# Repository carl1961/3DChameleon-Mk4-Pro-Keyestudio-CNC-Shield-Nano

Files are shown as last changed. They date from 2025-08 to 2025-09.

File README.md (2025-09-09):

# 3DChameleon-Mk4-Pro-Keyestudio-CNC-Shield-Nano
3DChameleon Mk4 Pro   

Controller using Keyestudio Nano CNC Shield V4 (Ks0152)  https://wiki.keyestudio.com/Ks0152_keyestudio_CNC_Shield_V4

WIN_20250906_18_50_13_Pro

WIN_20250828_07_41_26_Pro

3DChameleon_Mk4_Pro_Keyestudio_CNC_Shield_Nano v17

3DChameleon_Mk4_Pro_Keyestudio_CNC_Shield_Nano-2

## endstop micro switch 

Used for button on controller, in photo connected to Cool EN , later it will be moved to like X+ and external enstop switch on  X- those both share same D9 pin.

WIN_20250828_07_53_02_Pro

WIN_20250828_07_51_41_Pro

https://www.3dchameleon.com/old-forum/support/help-on-setup-for-cnc-shield-v4-ankermake-m5c

AMS Multi color for any 3d printer

https://github.com/3DChameleon/3DChameleonMk4

https://www.3dchameleon.com/

https://www.youtube.com/@3d_chameleon

Easy 3D Printable 4Y splitter    https://www.printables.com/model/808136-4-in-1-ptfe-adapter

Cutter Servo Board plugged into Z drive location 12V source,  stepdown to 6 Volts for servo using DD4OAJSA (adjustable ) 

!! Do voltage adjustment before plugging servo in.!!  https://alexnld.com/product/3pcs-dd40ajsa-5-40v-to-24v-12v-5v-wide-voltage-adjustable-step-down-dc-voltage-converter-power-regulator-module/

WIN_20250828_14_45_58_Pro

#Things to know

[Cotestant custom work !!](https://github.com/cotestatnt/3DChameleonMk4)

cotestatnt

I successfully built and installed a slightly modified version of the 3D Chameleon color changer on a Bambulab A1, and it works really well.
I can complete a color change in less than 20 seconds because the filament path on the A1 is very short. There is still room to improve this further, for example, by increasing the stepper motor speed.

The only aspect that didn’t fully convince me is the small teeth system for securing the PTFE tubes. So, I adapted your design to accommodate these fittings that I had available, cut in half:



(Connect Straight Union Tube Fitting, 4mm OD x 4mm OD, Straight Pneumatic Connector)

I believe there is also enough space to screw in a standard PC4-M6 fitting without any major issues.

For the electronics, I repurposed some components I had on hand, using a CNC shield for an Arduino Nano and a couple of Hall sensors instead of microswitches. I also added a sensor for homing the selector without bringing the motor to a mechanical stop, as I found it to be somewhat inaccurate—the motor tends to "bounce" when it starts skipping steps. While this isn’t a major issue, since I had the sensor available, I preferred this approach.
As for the firmware, since speed is more important to me than flexibility or the max number of possible colors, I simplified the color selection process, as I usually only need 2–3 colors for my designs.

## Jumpers and pins

KS0152_shield

## New Code by cotestatnt  https://github.com/cotestatnt/3DChameleonMk4

toolchange (Code in slicer pressing Hall sensor) or External button 

 selectionTime >= 500 && selectionTime < 1000)   Select extruder A

 selectionTime >= 1000 && selectionTime < 1500)  Select extruder B

 selectionTime >= 1500 && selectionTime < 2000)  Select extruder C
 
 selectionTime >= 2000 && selectionTime < 2500)  Select extruder D 

 selectionTime >= 3200)                          home sequence

 

## Selecter (Hall Sensor) 

tool_selector2

## KY-003 Hall Sensor



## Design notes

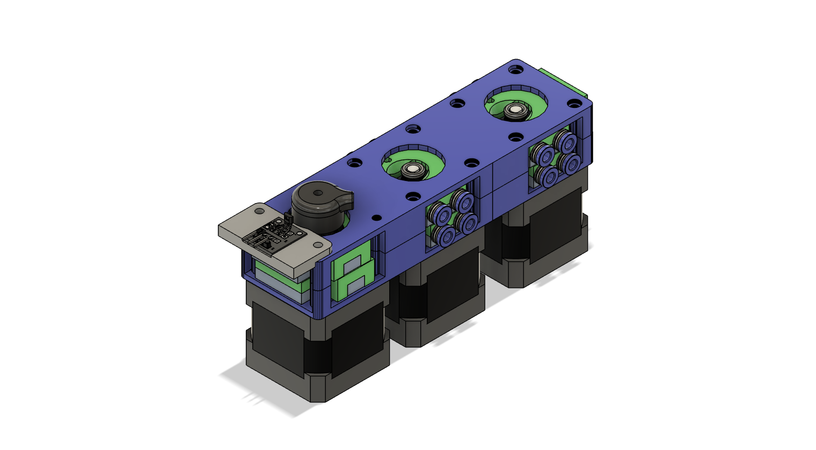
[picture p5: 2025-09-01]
3DChameleon-Mk4-8-Color v21.png

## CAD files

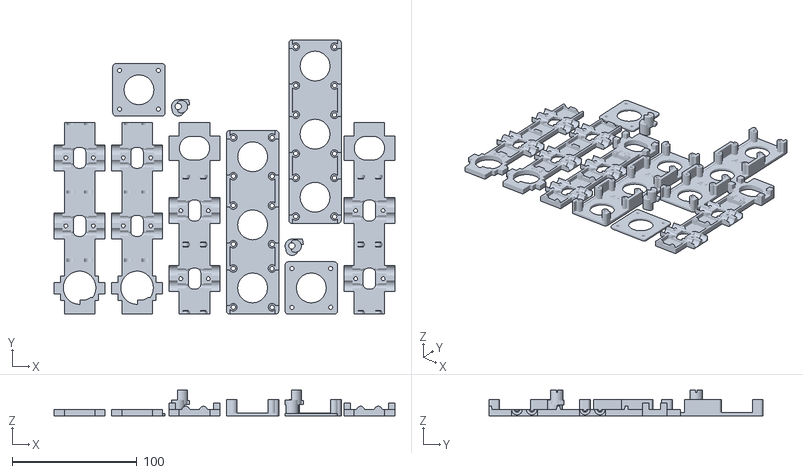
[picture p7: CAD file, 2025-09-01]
STL/3DChameleon 4.0 (8 color) (coupling)(FULL SET).stl
273.0 x 219.6 x 20.5

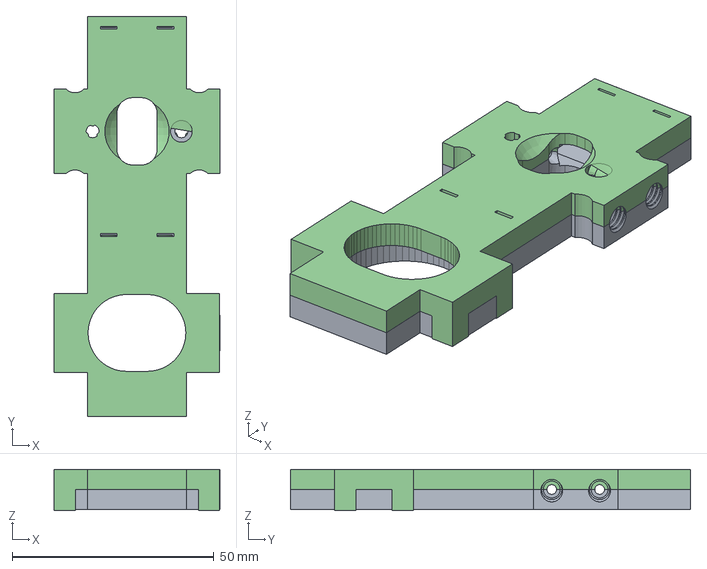
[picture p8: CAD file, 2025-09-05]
CAD/3DChameleon 4.0 (B Part C Part) (4 color) (PC4-M6).step
41.0 x 99.1 x 10.2 mm

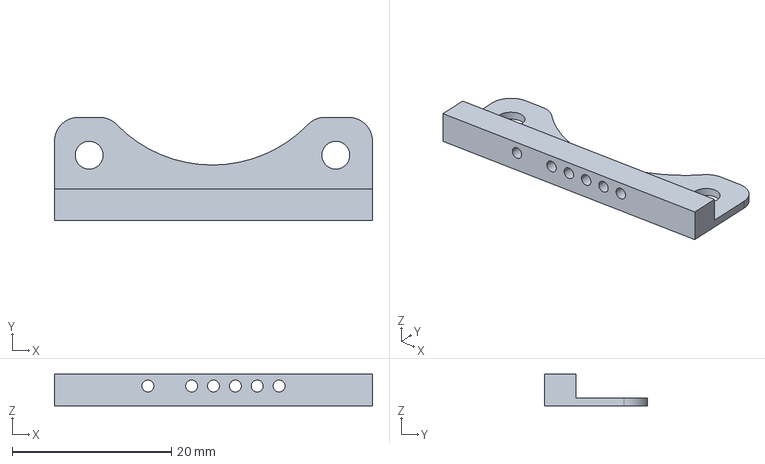
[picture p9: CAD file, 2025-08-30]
cotestatnt custom 3DChameleonMk4-main/3DChameleon (home sensor bracket).step
40.0 x 13.0 x 4.00 mm

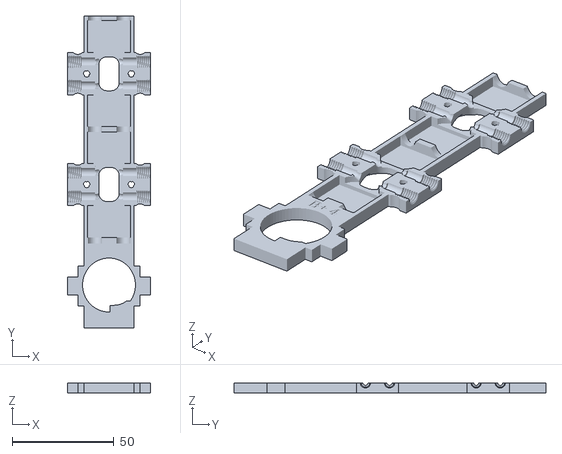
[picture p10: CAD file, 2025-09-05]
STL/3DChameleon 4.0 (B Part) (8 color) (PC4-M6).stl
41.0 x 153.6 x 5.00

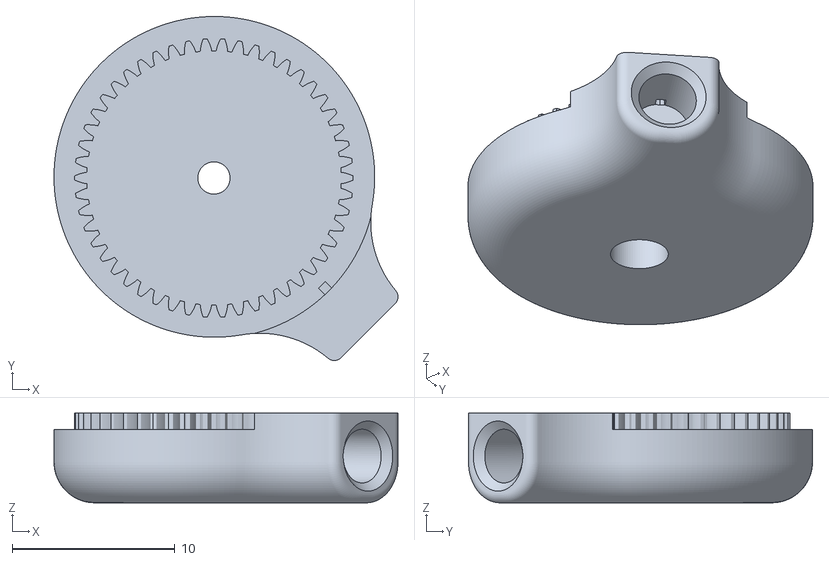
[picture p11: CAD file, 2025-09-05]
STL/Homing Parts/3DChameleon 4.0 (Magnet) (slip grooves).stl
21.1 x 21.1 x 5.50

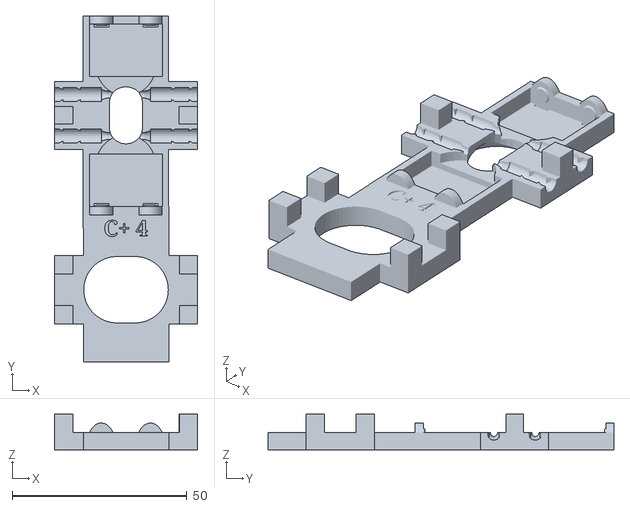
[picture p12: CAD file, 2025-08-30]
STL/Original/3DChameleon 4.0 (C Part).stl
41.0 x 99.1 x 10.2

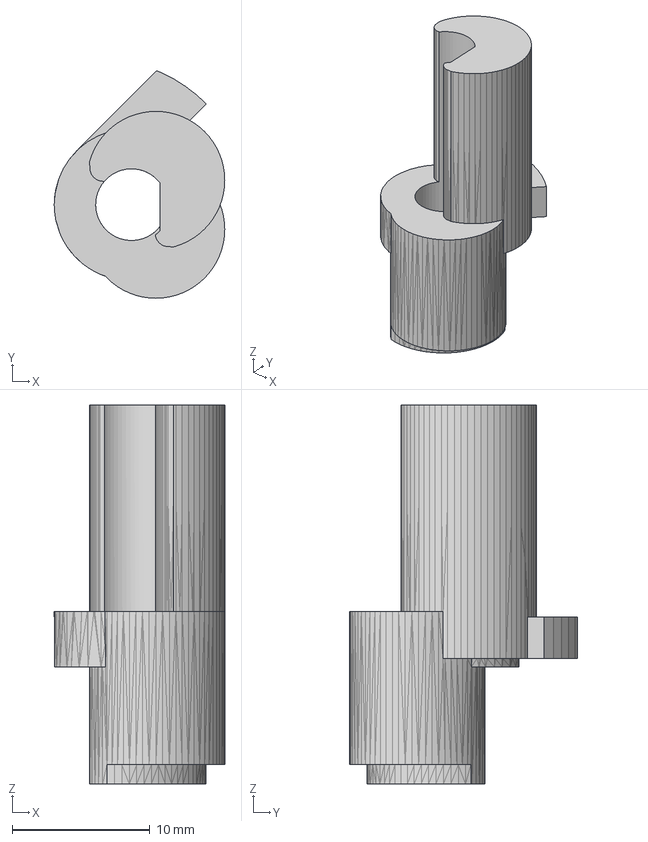
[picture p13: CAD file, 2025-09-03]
CAD/3DChameleon 4.0 (Cam) (Homing Magnet)_.step
12.4 x 16.5 x 27.5 mm

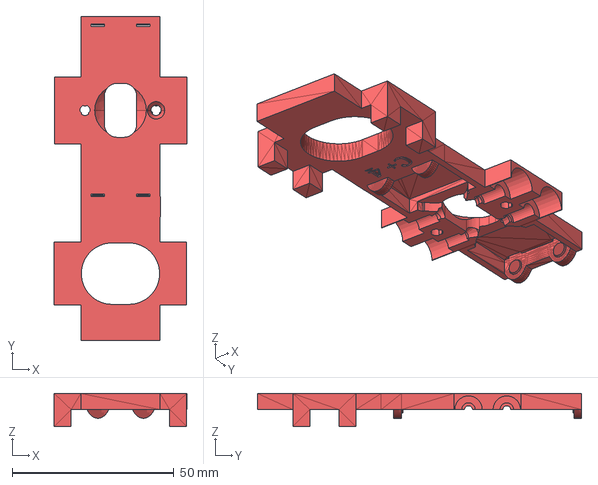
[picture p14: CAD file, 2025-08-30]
cotestatnt custom 3DChameleonMk4-main/3DChameleon 4.0 (C Part).step
41.0 x 100.3 x 10.2 mm

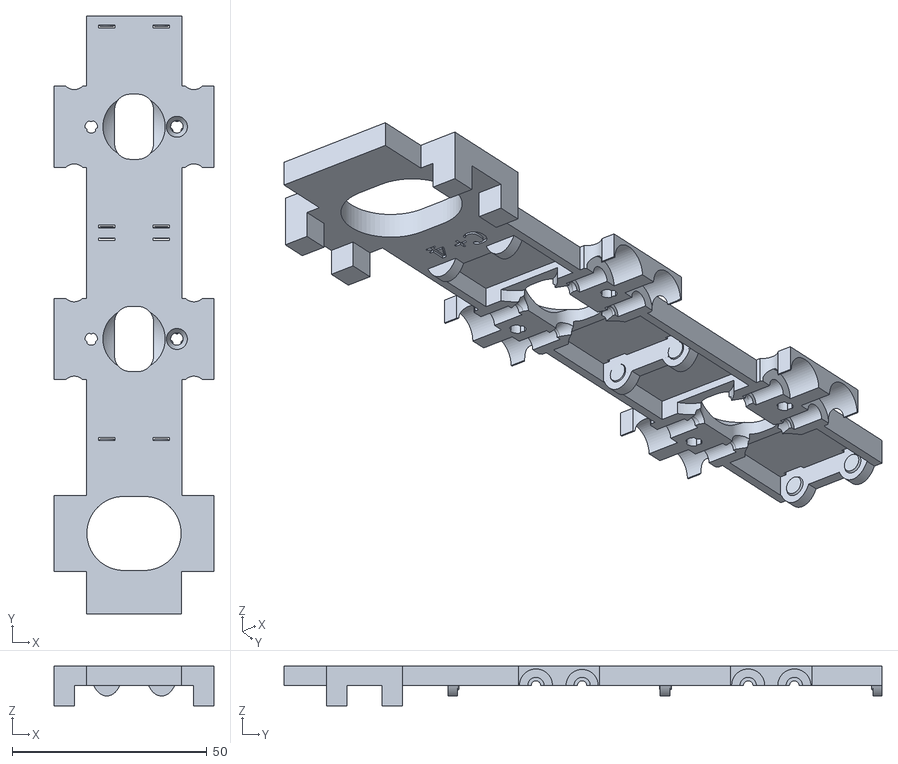
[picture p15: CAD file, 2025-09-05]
STL/3DChameleon 4.0 (C Part) (8 color) (couplings) V2.stl
41.0 x 153.6 x 10.2

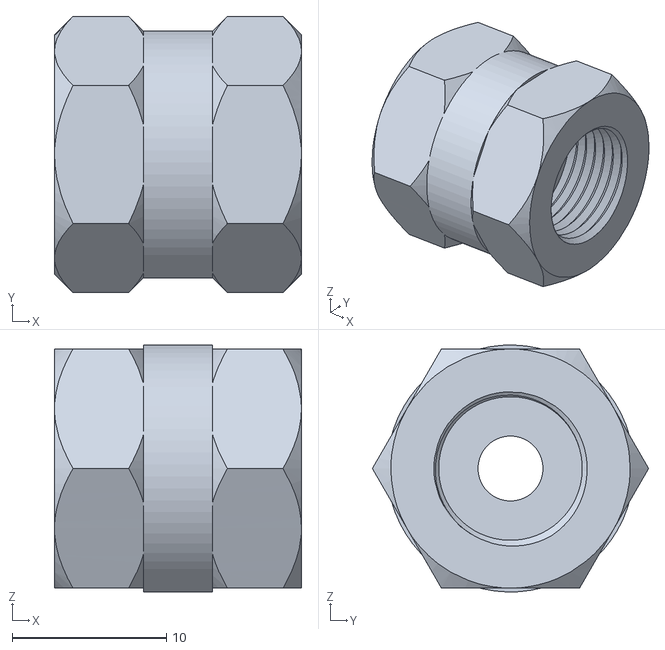
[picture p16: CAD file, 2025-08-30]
STL/Original/3DChameleon_PC4-M10_PTFE_Coupler.stl
16.0 x 17.9 x 16.0

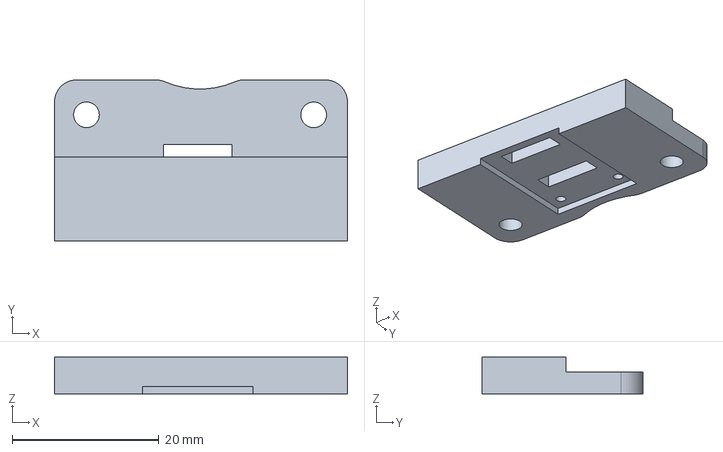
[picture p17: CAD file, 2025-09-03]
CAD/3DChameleon (home sensor bracket) v2.step
40.0 x 22.0 x 5.00 mm

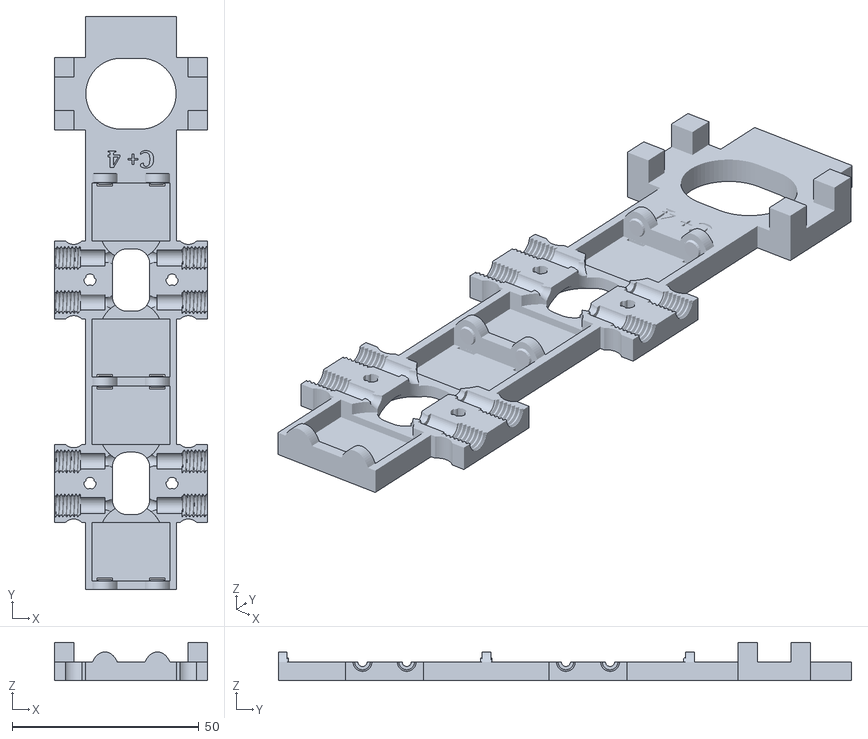
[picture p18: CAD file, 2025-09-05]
STL/3DChameleon 4.0 (C Part) (8 color) (PC4-M6).stl
41.0 x 153.6 x 10.2

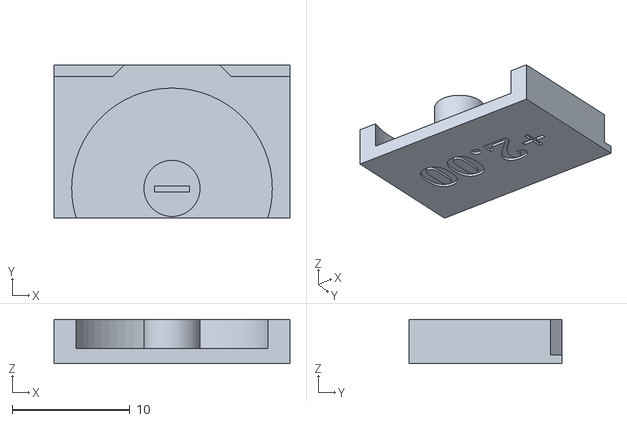
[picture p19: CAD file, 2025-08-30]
STL/Original/3DChameleon 4.0 (Bearing Carrier).stl
20.0 x 13.0 x 3.75

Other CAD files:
STL/Homing Parts/3DChameleon 4.0 (Magnet) (slip grooves)-V2.stl
cotestatnt custom 3DChameleonMk4-main/3DChameleon (home sensor bracket) v1.stl
STL/Homing Parts/3DChameleon 4.0 (Cam) (Magnet).stl
CAD/3DChameleon 4.0 (Magnet) (slip grooves) v2.step
cotestatnt custom 3DChameleonMk4-main/3DChameleon 4.0 (C Part) v1.stl
CAD/3DChameleon 4.0 (Magnet-Mount) (slip grooves) v2.step
STL/3DChameleon (home sensor bracket) v2.stl
STL/3DChameleon 4.0 (8 color) (coupling)(SET).stl
STL/3DChameleon 4.0 (A Part) (8 color).stl
STL/3DChameleon 4.0 (B Part) (4 color) (PC4-M6).stl
STL/3DChameleon 4.0 (B Part) (8 color) (coupling) V2.stl
STL/3DChameleon 4.0 (B Part) (8 color) (coupling).stl
STL/3DChameleon 4.0 (C Part) (4 color) (PC4-M6).stl
STL/3DChameleon 4.0 (C Part) (8 color) (couplings).stl
STL/3DChameleon 4.0 (C Part) (8 color).stl
STL/3DChameleon 4.0 (Cam) (v2).stl
STL/3DChameleon-Mk4-8-Color-Model.stl
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

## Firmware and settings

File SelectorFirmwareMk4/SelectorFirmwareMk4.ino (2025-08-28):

// November 28, 2024

/* 3DChameleon Mk4.1 Firmware

Copyright 2024 William J. Steele

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
Single Button Press Commands (count pulses of selector)

#1 - 1
#2 - 2
#3 - 3
#4 - 4
#5 - Home and Load
#6 - Unload Last and Home
#7 - Home
#8 - Next Filament
#9 - Random Filament
 
*/

#include <SSD1306Ascii.h> //i2C OLED
#include <SSD1306AsciiWire.h> //i2C OLED
#include <SparkFunSX1509.h> // sparkfun i/o expansion board - used for additional filament sensors as well as communications with secondary boards
#include <Wire.h>
#include <SPI.h>
#include <Servo.h>

#define SCREEN_WIDTH 128 // OLED display width, in pixels
#define SCREEN_HEIGHT 64 // OLED display height, in pixels

/**
 * Made with Marlin Bitmap Converter
 * https://marlinfw.org/tools/u8glib/converter.html
 *
 * This bitmap from 128x64 pasted image
 */
#pragma once

const unsigned char bitmap_logo[] PROGMEM = {
  B00000000,B00000000,B00000000,B00000000,B00000000,B00000000,B00000000,B00000000,B00000000,B00000000,B00000000,B00000000,B00000000,B00000000,B00000000,B00000000,
  B00000000,B00000000,B00000000,B00000000,B00000000,B00000000,B00000000,B00000000,B00000000,B00000000,B00000000,B00000000,B00000000,B00000000,B00000000,B00000000,
  B00000000,B00000000,B00000000,B00000000,B00000000,B00000000,B00000000,B00000000,B00000000,B00000000,B00000000,B00000000,B00000000,B00000000,B00000000,B00000000,
  B00000000,B00000000,B00000000,B00000000,B00000000,B00000000,B00000000,B00000000,B00000000,B00000000,B00000000,B00000000,B00000000,B00000000,B00000000,B00000000,
  B00000000,B00000000,B00000000,B00000000,B00000000,B00000000,B00000000,B00001000,B00000000,B00000000,B00000000,B00000000,B00000000,B00000000,B00000000,B00000000,
  B00000000,B00000000,B00000000,B00000000,B00000000,B00000000,B00110000,B00001100,B00100000,B00000000,B00000000,B00000000,B00000000,B00000000,B00000000,B00000000,
  B00000000,B00000000,B00000000,B00000000,B00000000,B00000000,B01111100,B00001110,B00110000,B00011100,B00000000,B00000000,B00000000,B00000000,B00000000,B00000000,
  B00000000,B00000000,B00000000,B00000000,B00000000,B00000000,B01111111,B00011111,B01111000,B00011111,B00000000,B00000000,B00000000,B00000000,B00000000,B00000000,
  B00000000,B00000000,B00000000,B00000000,B00000000,B00000000,B01111111,B10011111,B11111000,B00011111,B10000000,B00000000,B00000000,B00000000,B00000000,B00000000,
  B00000000,B00000000,B00000000,B00000000,B00000000,B00000000,B01111111,B11011111,B11110110,B00011111,B11000000,B00000000,B00000000,B00000000,B00000000,B00000000,
  B00000000,B00000000,B00000000,B00000000,B00000000,B00000000,B01111111,B10000000,B00000110,B00011111,B11100000,B00000000,B00000000,B00000000,B00000000,B00000000,
  B00000000,B00000000,B00000000,B00000000,B00000000,B11111100,B01111101,B11111111,B11110010,B00111111,B11110000,B00000000,B00000000,B00000000,B00000000,B00000000,
  B00000000,B00000000,B00000000,B00000000,B00000000,B11111111,B00001111,B11111111,B11111110,B00111111,B11111000,B00000000,B00000000,B00000000,B00000000,B00000000,
  B00000000,B00000000,B00000000,B00000000,B00000000,B01111111,B00111111,B11111111,B11111111,B00111111,B11111100,B00000000,B00000000,B00000000,B00000000,B00000000,
  B00000000,B00000000,B00000000,B00000000,B00000000,B01111110,B00111111,B11111111,B11111111,B01111111,B11111100,B00000000,B00000000,B00000000,B00000000,B00000000,
  B00000000,B00000000,B00000000,B00000000,B00000000,B01111101,B11111111,B11111111,B11111111,B01111111,B11111110,B00000000,B00000000,B00000000,B00000000,B00000000,
  B00000000,B00000000,B00000000,B00000000,B00000000,B01111011,B11111111,B11111111,B11111110,B11111111,B11111110,B00000000,B00000000,B00000000,B00000000,B00000000,
  B00000000,B00000000,B00000000,B00000000,B00000000,B01100111,B11101111,B11111111,B11111111,B11111111,B11111110,B00000000,B00000000,B00000000,B00000000,B00000000,
  B00000000,B00000000,B00000000,B00000000,B00000111,B10001111,B11110111,B11111111,B11111111,B11111111,B11111111,B00000000,B00000000,B00000000,B00000000,B00000000,
  B00000000,B00000000,B00000000,B00000000,B00001111,B10111111,B11111011,B11111111,B11111101,B11111110,B00011111,B00000000,B00000000,B00000000,B00000000,B00000000,
  B00000000,B00000000,B00000000,B00000000,B00001111,B10111111,B11111001,B11111111,B11111111,B11111100,B00001111,B00000000,B00000000,B00000000,B00000000,B00000000,
  B00000000,B00000000,B00000000,B00000000,B00001111,B01111111,B11111101,B11111111,B11111111,B11111001,B11110111,B00000000,B00000000,B00000000,B00000000,B00000000,
  B00000000,B00000000,B00000000,B00000000,B00000111,B11111111,B11111110,B11111111,B11111111,B11111011,B11110011,B00000000,B00000000,B00000000,B00000000,B00000000,
  B00000000,B00000000,B00000000,B00000000,B00000010,B11111111,B11111110,B11111111,B11111111,B11111011,B10111011,B00000000,B00000000,B00000000,B00000000,B00000000,
  B00000000,B00000000,B00000000,B00000000,B00111100,B11111111,B11111111,B01111111,B11111111,B11111011,B11110011,B00000000,B00000000,B00000000,B00000000,B00000000,
  B00000000,B00000000,B00000000,B00000000,B01111101,B11111111,B11111111,B01111111,B11111111,B11111001,B11110111,B00000000,B00000000,B00000000,B00000000,B00000000,
  B00000000,B00000000,B00000000,B00000000,B01111101,B11111111,B11111111,B10111111,B11111101,B11111100,B11101111,B00000000,B00000000,B00000000,B00000000,B00000000,
  B00000000,B00000000,B00000000,B00000000,B00111101,B11111111,B11111111,B10000000,B00000000,B11111111,B11011111,B00000000,B00000000,B00000000,B00000000,B00000000,
  B00000000,B00000000,B00000000,B00000000,B00011001,B11111111,B11111111,B10000000,B00000000,B11111111,B11111111,B00000000,B00000000,B00000000,B00000000,B00000000,
  B00000000,B00000000,B00000000,B00000000,B00001011,B11111111,B11111111,B01100000,B00000000,B01111111,B11111111,B00000000,B00000000,B00000000,B00000000,B00000000,
  B00000000,B00000000,B00000000,B00000000,B00000001,B11111111,B11111110,B11111000,B00000000,B00111111,B11111111,B00000000,B00000000,B00000000,B00000000,B00000000,
  B00000000,B00000000,B00000000,B00000000,B00011010,B01111111,B11111101,B11111110,B00000000,B00001111,B11111110,B00000000,B00000000,B00000000,B00000000,B00000000,
  B00000000,B00000000,B00000000,B00000000,B01111011,B11100111,B11111011,B11111110,B00000000,B00000111,B11111110,B00000000,B00000000,B00000000,B00000000,B00000000,
  B00000000,B00000000,B00000000,B00000000,B11111011,B11111100,B01110000,B01111111,B00000000,B00000001,B11111110,B00000000,B00000000,B00000000,B00000000,B00000000,
  B00000000,B00000000,B00000000,B00000000,B01111011,B11111111,B00000000,B01111111,B10000000,B00000000,B01111100,B00000000,B00000000,B00000000,B00000000,B00000000,
  B00000000,B00000000,B00000000,B00000000,B00011011,B11111111,B11000000,B11111111,B11111000,B00000000,B00000000,B00000000,B00000000,B00000000,B00000000,B00000000,
  B00000000,B00000000,B00000000,B00000000,B00001011,B11111111,B11100001,B11111111,B11111110,B00000000,B00000000,B00000000,B00000000,B00000000,B00000000,B00000000,
  B00000000,B00000000,B00000000,B00000000,B00111011,B11111111,B11100001,B11111111,B11111111,B00000000,B00000000,B00000000,B00000000,B00000000,B00000000,B00000000,
  B00000000,B00000000,B00000000,B00000000,B01111011,B11111111,B11100011,B11111111,B11110011,B10000000,B00000000,B00000000,B00000000,B00000000,B00000000,B00000000,
  B00000000,B00000000,B00000000,B00000000,B11111011,B11111111,B11100000,B00000001,B11111100,B00000000,B00000000,B00000000,B00000000,B00000000,B00000000,B00000000,
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
};


// Declaration for an SSD1306 display connected to I2C (SDA, SCL pins)
#define OLED_RESET  -1 // Reset pin # (or -1 if sharing Arduino reset pin)
#define OLED_I2C_ADDRESS 0x3C
SSD1306AsciiWire oled;

// define sparkfun io expansion
const byte SX1509_ADDRESS = 0x3E; // SX1509 I2C address
#define SX1509_FILAMENT_0 0
#define SX1509_FILAMENT_1 1
#define SX1509_FILAMENT_2 2
#define SX1509_FILAMENT_3 3
#define SX1509_OUTPUT 4
SX1509 io;                        // Create an SX1509 object to be used throughout


// defines pins numbers - Keyestudio Nano CNC shield v4 Board
#define extEnable 8
#define extStep 2
#define extDir 5

#define selEnable 8
#define selStep 3
#define selDir 6

#define trigger 9 //End Stop Switch (Black/White, do not connect red wire)  X+  Button X-
#define s_limit A4
#define filament A5

// defines pins numbers - 3D Chameleon Board
//#define extEnable 0
//#define extStep 1
//#define extDir 2

//#define selEnable A0
//#define selStep A1
//#define selDir A2

//#define trigger A3
//#define s_limit A4
//#define filament A5


const int counterclockwise = HIGH;
const int clockwise = !counterclockwise;

const int stepsPerRev = 200;
const int microSteps = 16;
const int speedDelay = 170;

const int defaultBackoff = 10;

Servo filamentCutter;  // create servo object to control a servo
int cutterPos = 0;    // variable to store the servo position
bool reverseServo = true;

int currentExtruder = -1;
int nextExtruder = 0;
int lastExtruder = -1;
int tempExtruder = -1;

int seenCommand = 0;
int prevCommand = 0;

int loaderMode = 2;  //(0= direct drive, 1=loader/unloader, 2=loader/unloader with press)

long triggerTime = 300;
long pulseTime = (triggerTime / 2);

long distance = 10;

long unloadDistance = stepsPerRev * microSteps * distance;  // this is 10 revs - about 10"
long loadDistance   = unloadDistance * 1.1;           // this is 11 revs - about 11"

int address = 0;
byte value;

long idleCount = 0;
bool logoActive = false;
bool T0Loaded = false;
bool T1Loaded = false;
bool T2Loaded = false;
bool T3Loaded = false;


bool displayEnabled = false;
bool ioEnabled = false;
//int sensorEnabled = 0;

long randomNumber = 0;

void setup()
{

  Wire.begin(); //start i2C  
	Wire.setClock(400000L); //set clock

  // set up IO expander
  if (io.begin(SX1509_ADDRESS) == true)
  {
    io.pinMode(SX1509_FILAMENT_0, INPUT_PULLUP);
    io.pinMode(SX1509_FILAMENT_1, INPUT_PULLUP);
    io.pinMode(SX1509_FILAMENT_2, INPUT_PULLUP);
    io.pinMode(SX1509_FILAMENT_3, INPUT_PULLUP);
    io.pinMode(SX1509_OUTPUT, OUTPUT);
    ioEnabled = true;
  }

  // enable OLED display
  oled.begin(&Adafruit128x64, OLED_I2C_ADDRESS);

  // wait for it to start up
  delay(50);
    

  // welcome screen
  oled.setFont(Adafruit5x7);
  oled.clear(); //clear display
	oled.println("");
  oled.println("       Welcome!"); //print a welcome message  
  oled.println("");
  oled.println("    3DChameleon Mk4"); //print a welcome message
  oled.println("");
  oled.println("         Pro");
  delay(3000);

  displayText(0, "       Ready!");
  
  seenCommand = 0;

  // Sets the two pins as Outputs
  pinMode(extEnable, OUTPUT);
  pinMode(extStep, OUTPUT);
  pinMode(extDir, OUTPUT);

  pinMode(selEnable, OUTPUT);
  pinMode(selStep, OUTPUT);
  pinMode(selDir, OUTPUT);

  // set up the button
  pinMode(trigger, INPUT_PULLUP);  // selector

  // a little override here... we're using the two inputs as I2C instead
  pinMode(s_limit, OUTPUT);    
  pinMode(filament, OUTPUT); 

  // lock the selector by energizing it
  digitalWrite(selEnable, HIGH);

  // make sure filament isn't blocked by gillotine
  connectGillotine();
  cutFilament();
  disconnectGillotine();
  
  prevCommand = 0;

}

int lastLoop = 0;

void loop()
{
  static uint32_t lastTime = 0;

  seenCommand = 0;
  idleCount++;

  // process button press
  if (digitalRead(trigger) == 0)
  {
    idleCount = 0;
    logoActive = false;
    unsigned long nextPulse;
    unsigned long pulseCount = 0;
    unsigned long commandCount = 0;

    // keep counting (and pulsing) until button is released
    while (digitalRead(trigger) == 0)
    {
      if(pulseCount<pulseTime)
      {
        pulseCount++;
        displayCommand(pulseCount);
        if(pulseCount>1) vibrateMotor();
      }
      delay(400);  // each pulse is 400+ milliseconds apart 
    }
    processCommand(pulseCount); // ok... execute whatever command was caught (by pulse count)
    pulseCount = 0;
  }

  // updates IO block, duh!  No really, grabs the state of the sparkfun gpio expansion
  updateIOBlock();

  // each loop adds 50ms delay, so that gets added AFTER the command is processed before the next one can start
  delay(50);
}

// read the sparkfun SX1509 io
void updateIOBlock()
{
    if(ioEnabled)
    {
      T0Loaded = io.digitalRead(SX1509_FILAMENT_0);
      T1Loaded = io.digitalRead(SX1509_FILAMENT_1);
      T2Loaded = io.digitalRead(SX1509_FILAMENT_2);
      T3Loaded = io.digitalRead(SX1509_FILAMENT_3);
    }
}

// display command for each button pulse
void displayCommand(long commandCount)
{

  switch(commandCount)
  {
  case 2:
    displayText(25, "    Switch to T0");
    break;
  case 3:
    displayText(25, "    Switch to T1");
    break;
  case 4:
    displayText(25, "    Switch to T2");
    break;
  case 5:
    displayText(25, "    Switch to T3");
    break;
  case 6:
    displayText(25, "    Home/Load T0");
    break;
  case 7:
    displayText(28, "    Unload/Home");
    break;
  case 8:
    displayText(50, "        Home");
    break;  
  case 9:
    displayText(50, "        Next");
    break;
  case 10:
    displayText(40, "       Random");
    break;
  default:
    displayText(30, "     No Command");
    break;
  }
}

// execute the pulse count command
void processCommand(long commandCount)
{

  // select case for commands
  switch (commandCount)
  {
  case 2: // unload current, switch to #0, load
    displayText(30, "     T0 Selected");
    currentExtruder = 0;
    processMoves();
    displayText(35, "      Idle - T0");
    break;

  case 3: // unload current, switch to #1, load
    displayText(30, "     T1 Selected");
    currentExtruder = 1;
    processMoves();
    displayText(35, "      Idle - T1");
    break;

  case 4: // unload current, switch to #3, load
    displayText(30, "     T2 Selected");
    currentExtruder = 2;
    processMoves();
    displayText(35, "      Idle - T2");
    break;

  case 5: // unload current, switch to #4, load
    displayText(30, "     T3 Selected");
    currentExtruder = 3;
    processMoves();
    displayText(35, "      Idle - T3");
    break;

  case 6: //home and reload #1
    displayText(40, "      Homing...");
    homeSelector();
    displayText(15, "   Press to Load T0");
    gotoExtruder(0, 0);
    if(loaderMode>0)rotateExtruder(clockwise, loadDistance);
    if(loaderMode>0)gotoExtruder(0, 1);
    currentExtruder = 0;
    lastExtruder = 0;
    displayText(35, "      Idle - T0");
    break;
    
  case 7: // unload current and rehome selector
    displayText(30, "     Cutting...");
    connectGillotine();
    cutFilament();
    switch(lastExtruder)
    {
      case 0:
        displayText(10, "  Press to Unload T0");
        break;
      case 1:
        displayText(10, "  Press to Unload T1");
        break;
      case 2:
        displayText(10, "  Press to Unload T2");
        break;
      case 3:
        displayText(10, "  Press to Unload T3");
        break;
    } 
    if(loaderMode>0)gotoExtruder((lastExtruder==3?2:lastExtruder+1),lastExtruder);
    if(lastExtruder<2)
    {
      if(loaderMode>0)rotateExtruder(counterclockwise, unloadDistance);
    }
    else
    {
      if(loaderMode>0)rotateExtruder(clockwise, unloadDistance);
    }
    disconnectGillotine();
    displayText(50, "        Idle");
    break;

  case 8:  
    displayText(40, "     Homing...");
    homeSelector();
    displayText(50, "        Idle");
    break;

  case 9: // move to next available filament
    displayText(30, "     Cutting...");
    connectGillotine();
    cutFilament();
    displayText(30, "     Next Tool");
    currentExtruder++;
    if(currentExtruder==4)currentExtruder=0;
    processMoves();
    displayText(35, "        Idle");
    break;

  case 10: // move to a random filament
    displayText(30, "     Cutting...");
    connectGillotine();
    cutFilament();
    displayText(30, "    Random Tool");

    // select a random number
    randomNumber = random(0,2) + 1;

    // skip ahead that many tools
    for(long i=0; i<randomNumber; i++)
    {
      currentExtruder++;
      if(currentExtruder==4)currentExtruder=0;
    }
    processMoves();
    displayText(50, "        Idle");
    break;
    
  default:
    displayText(47, "       Clear");
    delay(200);

    displayText(50, "        Idle");
    break;
  }
}

// just the routine to update the OLED
void displayText(int offset, String str)
{

  //if(displayEnabled){
    oled.clear();
    oled.println("");
    oled.println("   3DChameleon Mk4"); //print a welcome message
    oled.println("");
    oled.println("");
    oled.println(str);
    oled.println("");
    oled.println("");
    if(ioEnabled)
    {
      oled.print("     ");
      if(T0Loaded)
      {
        oled.print("0  ");
      }
      else
      {
        oled.print("+  ");
      }
      if(T1Loaded)
      {
        oled.print("1  ");
      }
      else
      {
        oled.print("+  ");
      }
      if(T2Loaded)
      {
        oled.print("2  ");
      }
      else
      {
        oled.print("+  ");
      }
      if(T3Loaded)
      {
        oled.println("3");
      }
      else
      {
        oled.println("+");
      }
    }
    else
    {
      oled.println("     -  -  -  -");
    }
  //  }
}

// real work is here
void processMoves()
{

  // make sure we have a real extruder selected
  if(lastExtruder>-1)
  {

    // if so, we need to cut the filament
    displayText(30, "     Cutting...");
    connectGillotine();
    cutFilament();

    // ok... then wait for the 2nd button press to unload it
    switch(lastExtruder)
    {
      case 0:
        displayText(10, "  Press to Unload T0");
        break;
      case 1:
        displayText(10, "  Press to Unload T1");
        break;
      case 2:
        displayText(10, "  Press to Unload T2");
        break;
      case 3:
        displayText(10, "  Press to Unload T3");
        break;
    } 

    // roll over to first if on last
    if( loaderMode>0 ) gotoExtruder( ( lastExtruder==3 ? 2 : (lastExtruder+1)), lastExtruder);

    // this determines which direction to move the motor, 0-1 : counterclockwise, 2-3 : clockwise
    if(lastExtruder<2)
    {
      if(loaderMode>0)rotateExtruder(counterclockwise, unloadDistance);
    }
    else
    {
      if(loaderMode>0)rotateExtruder(clockwise, unloadDistance);
    }
  }
  else
  {
    lastExtruder = 0;
  }
  disconnectGillotine();
  
  // tell it to actually execute that command now
  gotoExtruder(lastExtruder, currentExtruder);

  // ok... filament unloaded, time to load the new... so tell the user
  switch(currentExtruder)
  {
    case 0:
      displayText(15, "   Press to Load T0");
      break;
    case 1:
      displayText(15, "   Press to Load T1");
      break;
    case 2:
      displayText(15, "   Press to Load T2");
      break;
    case 3:
      displayText(15, "   Press to Load T3");
      break;
  }

  // same (but inversed) logic for motor direction
  if(currentExtruder<2)
  {
    if(loaderMode>0)rotateExtruder(clockwise, loadDistance);
  }
  else
  {
    if(loaderMode>0)rotateExtruder(counterclockwise, loadDistance);
  }

  // if we're loading, then load it now
  if(loaderMode>0)gotoExtruder(currentExtruder, (currentExtruder==3?2:currentExtruder+1));

  // everybody remember where we parked!
  lastExtruder = currentExtruder;
}


// this function simply moves from the currentCog to the targetCog is the best way
void gotoExtruder(int currentCog, int targetCog)
{
 
  int newCog = targetCog - currentCog;

  // ok... which way
  int newDirection = counterclockwise;
  if(newCog<0)
  {
    // we need to move the other way
    newDirection = clockwise;

    //and since we know we went too far... let's go the other way in steps as well
    newCog = currentCog - targetCog;
  }

  // if we're already on the current cog, then do nothing
  if(newCog > 0)
  {    
    // advance tool targetCog times
    for(int i=0; i<newCog; i++)
    {
      rotateSelector(newDirection, (stepsPerRev / 4) * microSteps);
    }
  }
}

// move the extruder motor in a specific direction for a specific distance (unless it's a "until button is not pressed")
void rotateExtruder(bool direction, long moveDistance)
{
  // note to bill:  make this acecelerate so it's very fast!!!
  
  digitalWrite(extEnable, LOW);  // lock the motor
  digitalWrite(extDir, direction); // Enables the motor to move in a particular direction
  const int fastSpeed = speedDelay/2; // double time

  // this is depricated right now... might bring it back in the future
  if(loaderMode==1)
  {

    // Makes 50 pulses for making one full cycle rotation
    for (long x = 0; x < (moveDistance-1); x++)
    {
      // this is how we pulse the motor to get it to step
      digitalWrite(extStep, HIGH);
      delayMicroseconds(fastSpeed);
      digitalWrite(extStep, LOW);
      delayMicroseconds(fastSpeed);
    }

  }

  if(loaderMode==2)
  {

   // keep waiting until button is pressed
   while (digitalRead(trigger) != 0)
    {
      delay(50);
    }
    
    // Move while button is pressed
    while (digitalRead(trigger) == 0)
    {

      // this is how we pulse the motor to get it to step
      digitalWrite(extStep, HIGH);
      delayMicroseconds(fastSpeed);
      digitalWrite(extStep, LOW);
      delayMicroseconds(fastSpeed);
    }
  }
  // ok, done pressing button, so make sure we're not energized (high is no, low is yes)
  digitalWrite(extEnable, HIGH);
}

// similar to extruder, but only stepping 50 (of 200) at a time
void rotateSelector(bool direction, int moveDistance)
{

  // while we are at it... can we make this faster using the magic you invented above?
  
  digitalWrite(selEnable, LOW); // lock the selector
  digitalWrite(selDir, direction); // Enables the motor to move in a particular direction

    // Makes 50 pulses for making one full cycle rotation
    for (int x = 0; x < (moveDistance-1); x++)
    {
      digitalWrite(selStep, HIGH);
      delayMicroseconds(speedDelay);
      digitalWrite(selStep, LOW);
      delayMicroseconds(speedDelay);
    }
}
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

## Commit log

2025-08-28 updated files
    added files
    [3DChameleon_Mk4_Pro_Keyestudio_CNC_Shield_Nano_Box.stl, 3DChameleon_Mk4_Pro_Keyestudio_CNC_Shield_Nano_Box_OLED_Cover_wSwitch.stl, Button.stl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]
2025-08-28 Update SelectorFirmwareMk4.ino
    Button and Trigger switch on X+ X- both share pin 9 (D9)
2025-08-30 added files
    added cotestatnt custom 3DChameleonMk4
    [3DChameleon (home sensor bracket) v1.stl, 3DChameleon (home sensor bracket).step, 3DChameleon 4.0 (B Part) v1.stl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]
2025-08-30 added step and cad files
    [3DChameleon 4.0 (B Part) (8 color) (coupling).stl, 3DChameleon 4.0 (C Part) (8 color) (couplings).stl]
2025-08-30 updated files
    [3DChameleon 4.0 (B Part) (8 color) (coupling).stl]
2025-09-01 updated files
    Homing parts
    [3DChameleon (home sensor bracket) v2.stl, 3DChameleon 4.0 (Cam) (Magnet).stl, 3DChameleon 4.0 (Cam) (v2).stl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]
2025-09-01 homing parts folder
    [3DChameleon 4.0 (Cam) (Magnet).stl, 3DChameleon 4.0 (Magnet) (slip grooves).stl, 3DChameleon 4.0 (Magnet) .stl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]
2025-09-01 added model
    [3DChameleon-Mk4-8-Color v8.step, 3DChameleon-Mk4-8-Color-Model.stl]
2025-09-03 Added Files
    PC4-M6 Parts
    [3DChameleon (home sensor bracket) v2.step, 3DChameleon 4.0 (B Part) (8 color) (PC4-M6) .stl, 3DChameleon 4.0 (C Part) (8 color) (PC4-M6) .stl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]
2025-09-04 added files
    3DChameleon 4.0 (B Part) (4 color) (PC4-M6) .stl
    3DChameleon 4.0 (A Part) (4 color) (PC4-M6) .stl
    [3DChameleon cotestatnt 4.0 (B Part)-PC4-M6.stl, 3DChameleon cotestatnt 4.0 (C Part)-PC4-M6.stl]
2025-09-04 added missing files
    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
    [3DChameleon 4.0 (B Part) (PC4-M6).stl, 3DChameleon 4.0 (C Part) (PC4-M6).stl]
2025-09-05 updated parts
    [3DChameleon 4.0 (B Part) (8 color) (PC4-M6) .stl, 3DChameleon 4.0 (C Part) (8 color) (PC4-M6) .stl, 3DChameleon 4.0 (C Part) (8 color) (PC4-M6).stl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]
2025-09-05 Replaced and added files
    [3DChameleon (home sensor bracket) v2.stl, 3DChameleon 4.0 (B Part C Part) (4 color) (PC4-M6).step, 3DChameleon 4.0 (B Part) (4 color) (PC4-M6).stl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]
2025-09-05 removed old files
    [3DChameleon 4.0 (B Part) (PC4-M6).stl, 3DChameleon 4.0 (C Part) (PC4-M6).stl, 3DChameleon 4.0 (B Part C Part) (4 color) (PC4-M6).step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]
